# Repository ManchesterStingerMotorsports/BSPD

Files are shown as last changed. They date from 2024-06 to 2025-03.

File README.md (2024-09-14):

# BSPD (Brake System Plausibility Device)

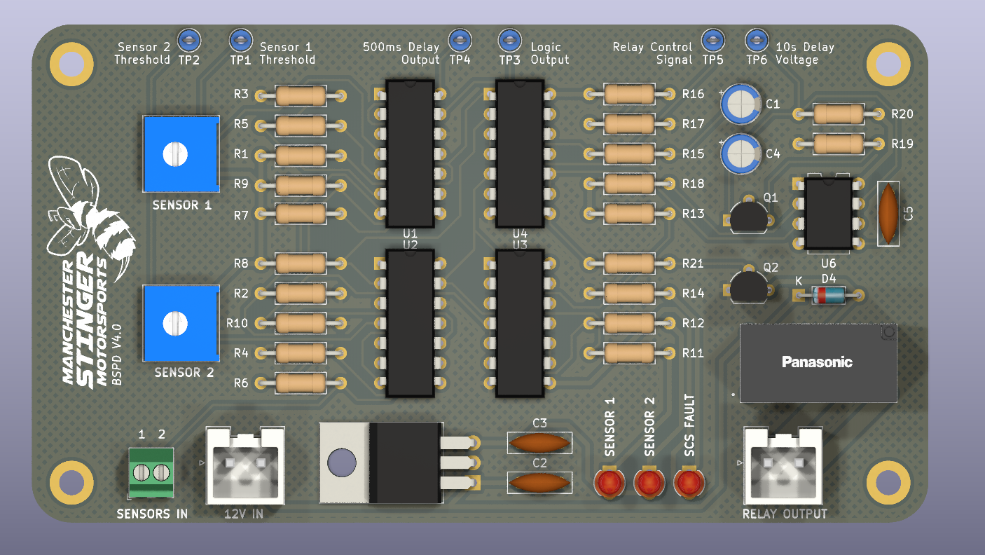
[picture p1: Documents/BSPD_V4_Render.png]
V4.0


[**FULL SCHEMATIC**](Documents/BSPD_V4_Schematic.pdf)

## Working Principle

The diagram below shows how the bspd would work (NOT the actual schematic)

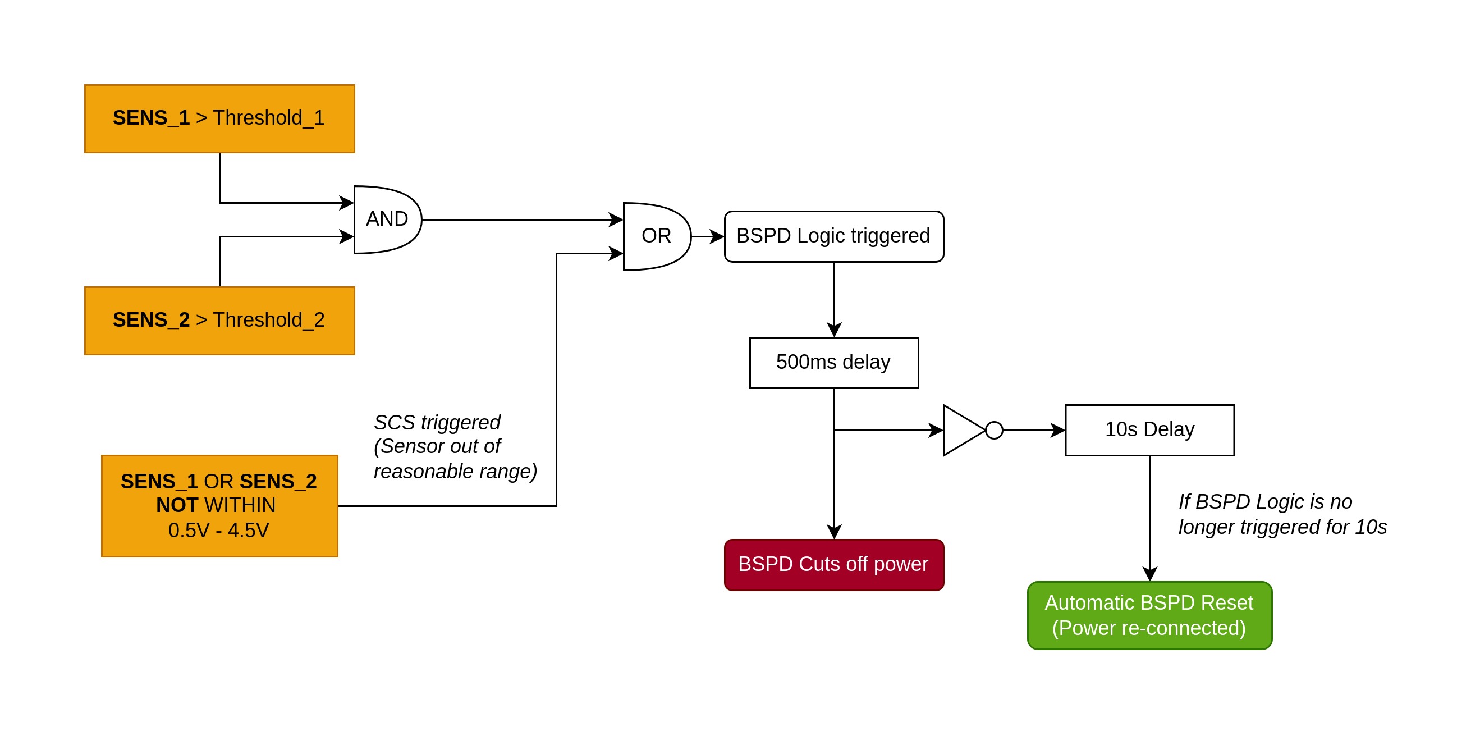
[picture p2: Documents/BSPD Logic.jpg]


- If both sensors' voltage are above the threshold voltage (set using the potentiometer) **or** SCS is triggered -> the bspd will cut off power.
- The delay only triggeres when the input signal is ON for the whole duration (eg, a 200ms signal will be rejected by the 500ms delay)
- The bspd will automatically reset once the triggering signal is no longer present for 10s

## Troubleshooting

There are 3 LEDs and 6 testpoints to be used when troubleshooting

- Sensor 1 or 2 LED turns ON 
  - **CAUSE:** The sensor voltage of 1 or 2 is higher than the threshold
  - Adjust the potentiometer to set the correct voltage threshold while measuring the voltage on TP1 and TP2 (Voltage on the test points should change as the potentiometer is turned).
  - Measure the input sensor voltage (Make sure the sensor is working)

- SCS LED turns ON
  - **CAUSE:** One of the sensors' voltage are outside the range of 0.5V to 4.5V
  - Make sure both sensors are connected (if one of the sensor is disconnected it will trigger the SCS).
  - Measure both sensors voltage to be within the range of 0.5V to 4.5V
  - Try to connect a 2.5V signal to both of the sensor input (The LED should turn off).
  - If all fails, there might be a fault on the scs circuit

- BSPD not resetting after 10s
  - Disconnect anything connected to TP6 (if theres any)
  - Make sure none of the LED is on during the 10s duration
  - Try to test the normal operation of the bspd to ensure that only the 10s delay is not working (chances are there might be other fault that is causing this)

## Important Notes

- For test point 6, TP6 (10s Delay Voltage), probing the point will affect the duration of the 10s delay. This is due to the use of a 1 Mega ohm resistor which is the range of most oscilloscope/multimeter input resistance. Using a 1X probe with an oscilloscope can even prevent the delay from working at all. So, **do not use the TP6 to measure the delay**, instead just use TP5 which is essentially the delay output.
- When manufacturing the board with the uni, have fun finding super small hidden shorted traces (possibly one under silkscreen). For some reason most of the BSPD boards made by the uni always have their own faults so, save yourself from a future headache by testing out the board slowly as you assemble them. **Removing copper pours might help so please remove it for the next revision.**

## Design Choices

Some parts of the schematic might need some extra explanation:

- The comparator LM339 can only reliably compare signals if one signal above 3V (refer the datasheet, look at "common mode range"), so to check for the 4.5V threshold, a voltage divider is used to scale down the input by half.
- The outputs of the comparator is connected together for SCS check since it is an open-drain output which basically OR gate all the outputs together
- The 10s timer uses a 555 monostable retriggerable circuit which we just realised that there is a dedicated IC that does the same thing. Something like SN74LVC1G123, which you might consider for future revision.

## Version Changelog

**V1.0**
- First Routed PCB

**V1.1**
- Changed R26 to 4.7k to limit current to base of the BJT controlling the relay

**V2.0**

- Changes are made after feedback from Dr. Theo
- Changed 500ms timer resistor to 430k with the assumption of 1% tolerence (Expected = 516ms, Min = 511ms, Max = 521ms)
- Changed the current limiting resistors from 470 to 4.7k to limit current to less than 1 mA (NAND gate limit)
- Removed copper pad on the mounting holes and added clearance from other copper pads
- Fixed ground routing loop on the PCB
- Smaller hatched copper pours
- Removed redundant voltage divider for SCS voltage reference

**V3.0**
- Replaced 5V supply input with 12V supply input
- Added 5V Voltage Regulator with capacitors
- Team logo added

**V4.0**
- Changed 5V Reg to a more common LM7805
- Changed transistors footprint to a bigger seperation pads footprint due to uni fabrication limitation
- Changed trimmer to a bigger but more common equivalent alternative
- Added diode for reverse relay coil voltage protection 
- PCB Routing optimised
- Added test points for easier troubleshooting

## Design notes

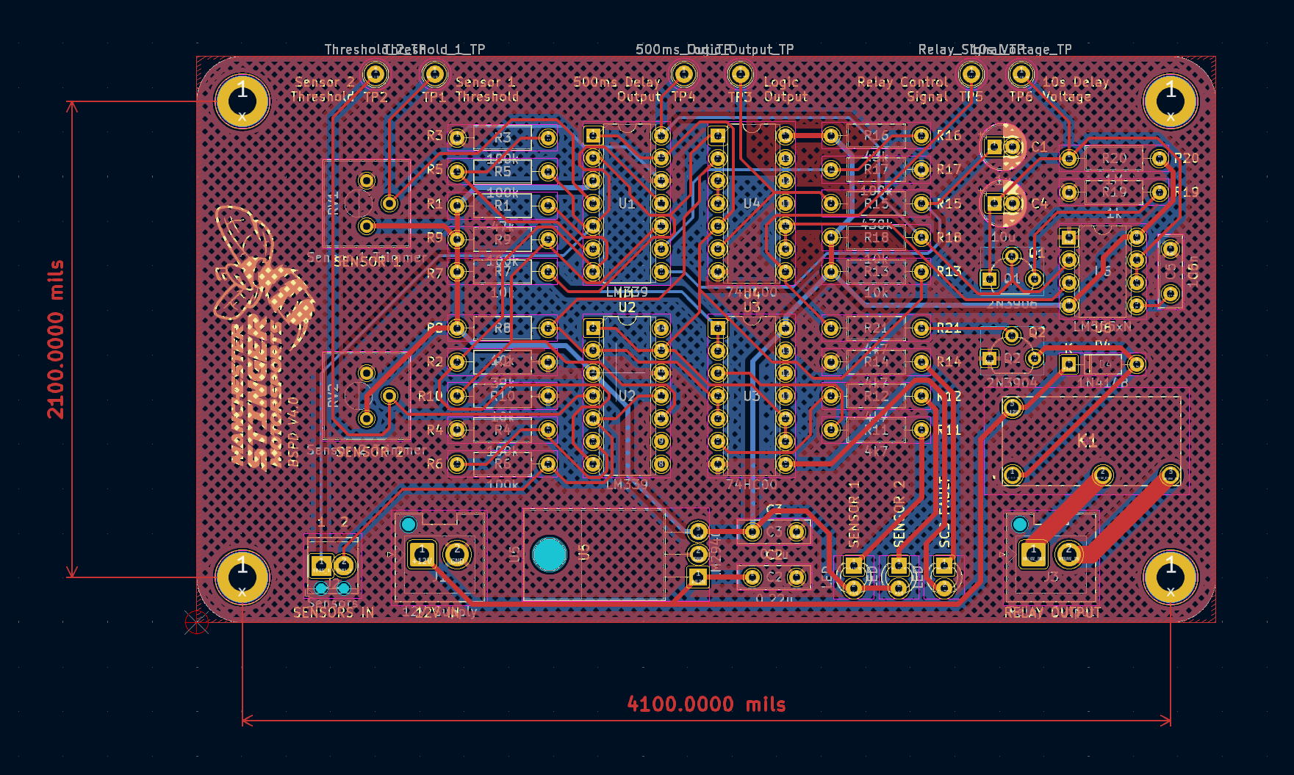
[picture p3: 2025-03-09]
Documents/BSPD Dimensions.png

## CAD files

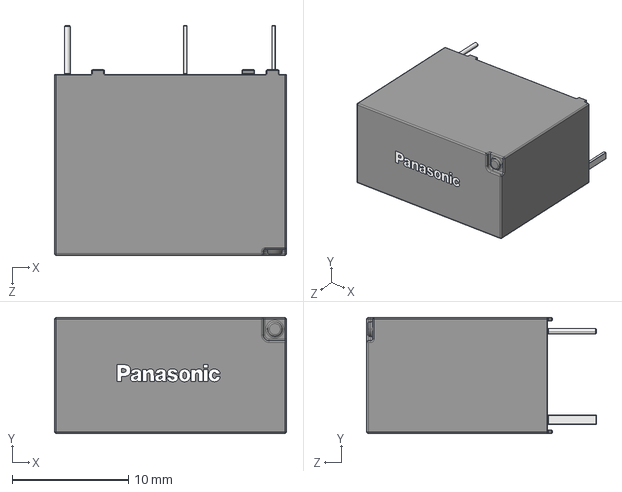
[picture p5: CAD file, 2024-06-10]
BSPD PCB/footprints/3D/ALQ3F12.stp
20.0 x 10.0 x 19.8 mm
ALQ305
Panasonic_Logo_5mm

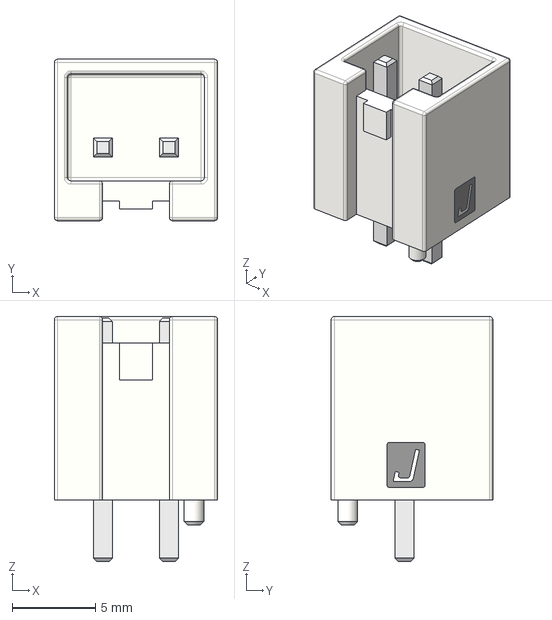
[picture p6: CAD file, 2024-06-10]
BSPD PCB/footprints/3D/B2P-VH-FB-B_LF__SN_.stp
9.80 x 9.70 x 14.7 mm

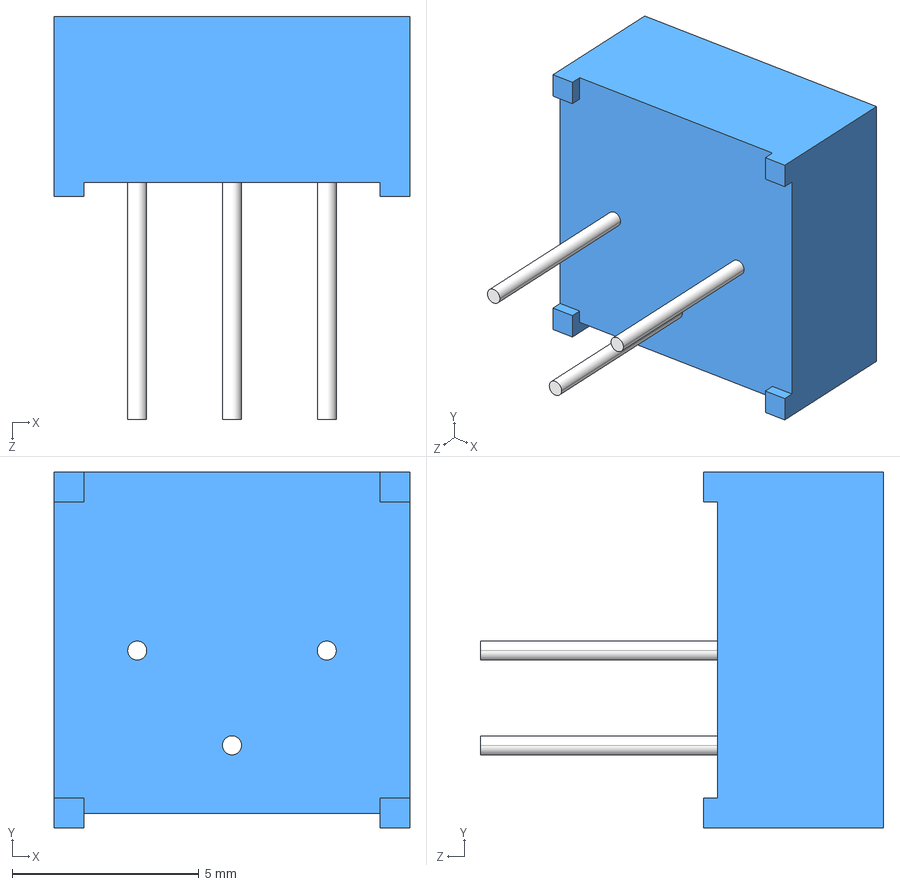
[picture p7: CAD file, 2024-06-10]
BSPD PCB/footprints/3D/3386P-1-500LF.stp
9.53 x 9.53 x 10.8 mm

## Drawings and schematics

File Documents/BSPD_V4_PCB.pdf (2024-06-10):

1 | 2 | 3 | 4 | 5 | 6

A

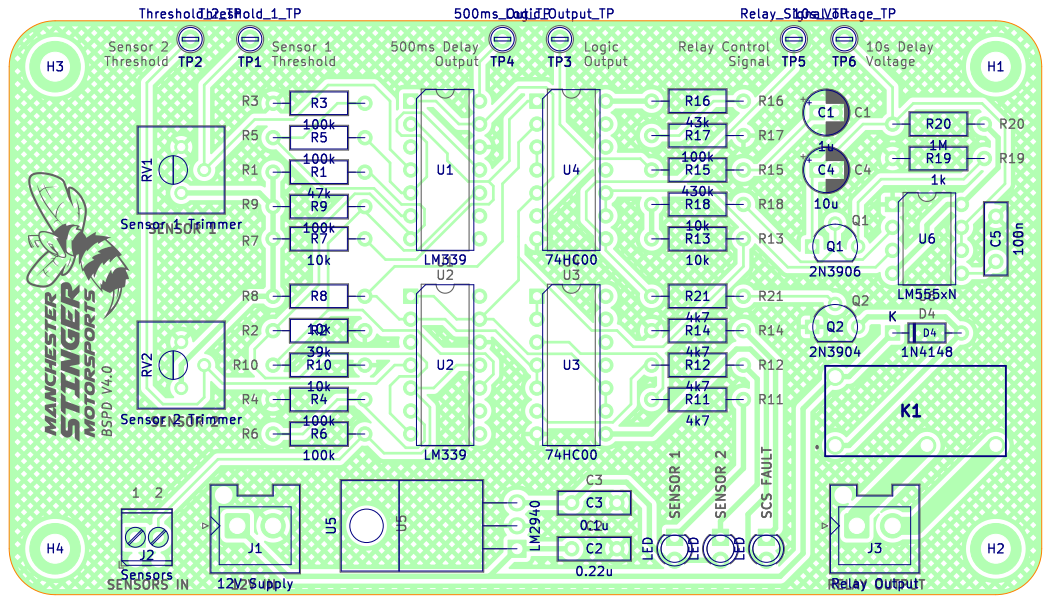
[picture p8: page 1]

Logic Output Sensor 2 Threshold

1 | 2 | 3 | 4 | 5 | 6

A

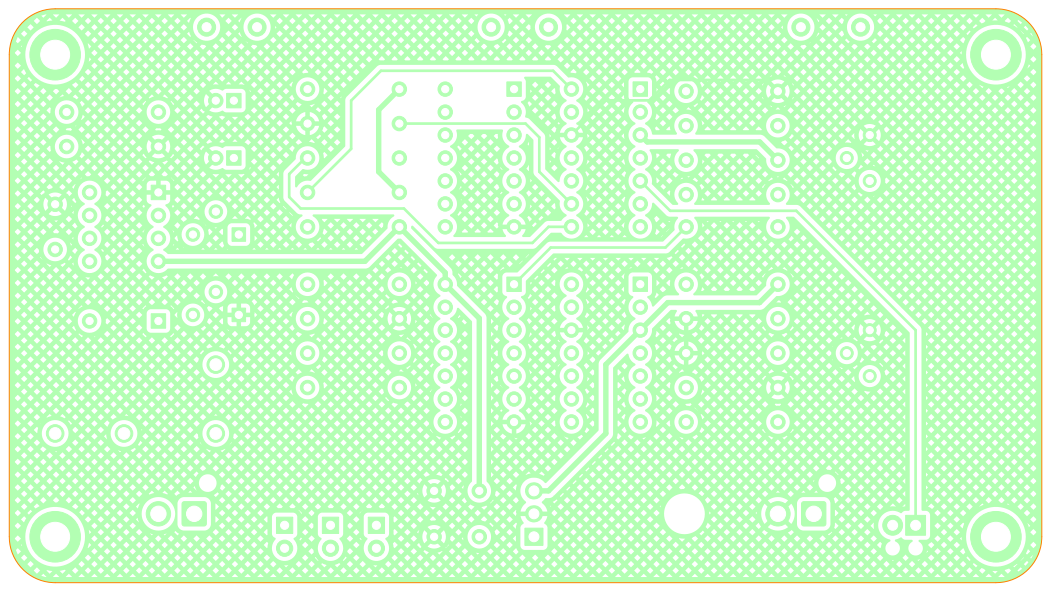
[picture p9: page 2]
D Date: 2024-06-10 KiCad; kicad; 7.0.8 Size: A4; Rev: V4.0; File: BSPD_ManchesterStingerMotorsports.kicad_pcb Sheet: Manchester Stinger; Motorsports

Id: 1/1 Title: BPSD

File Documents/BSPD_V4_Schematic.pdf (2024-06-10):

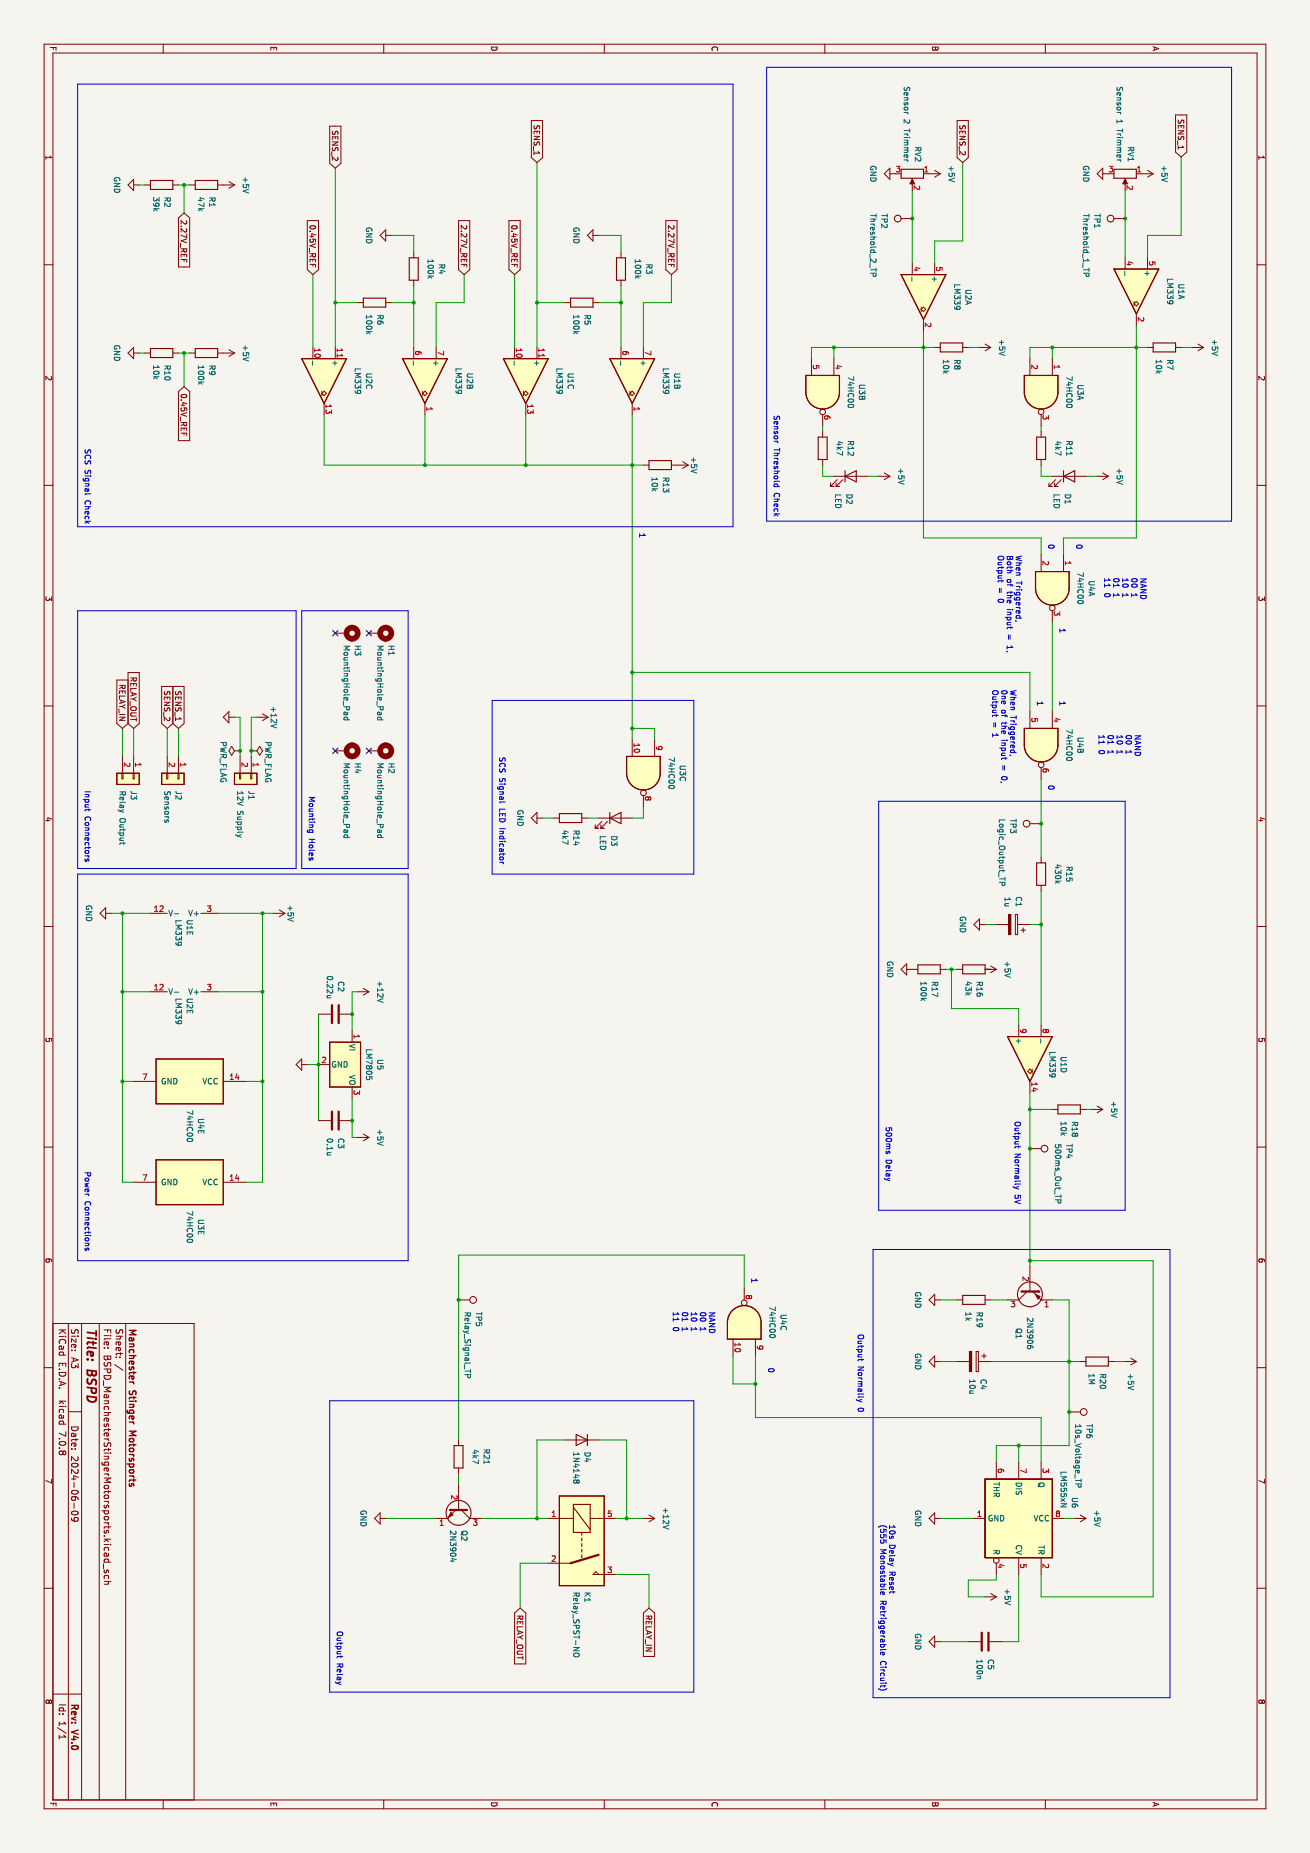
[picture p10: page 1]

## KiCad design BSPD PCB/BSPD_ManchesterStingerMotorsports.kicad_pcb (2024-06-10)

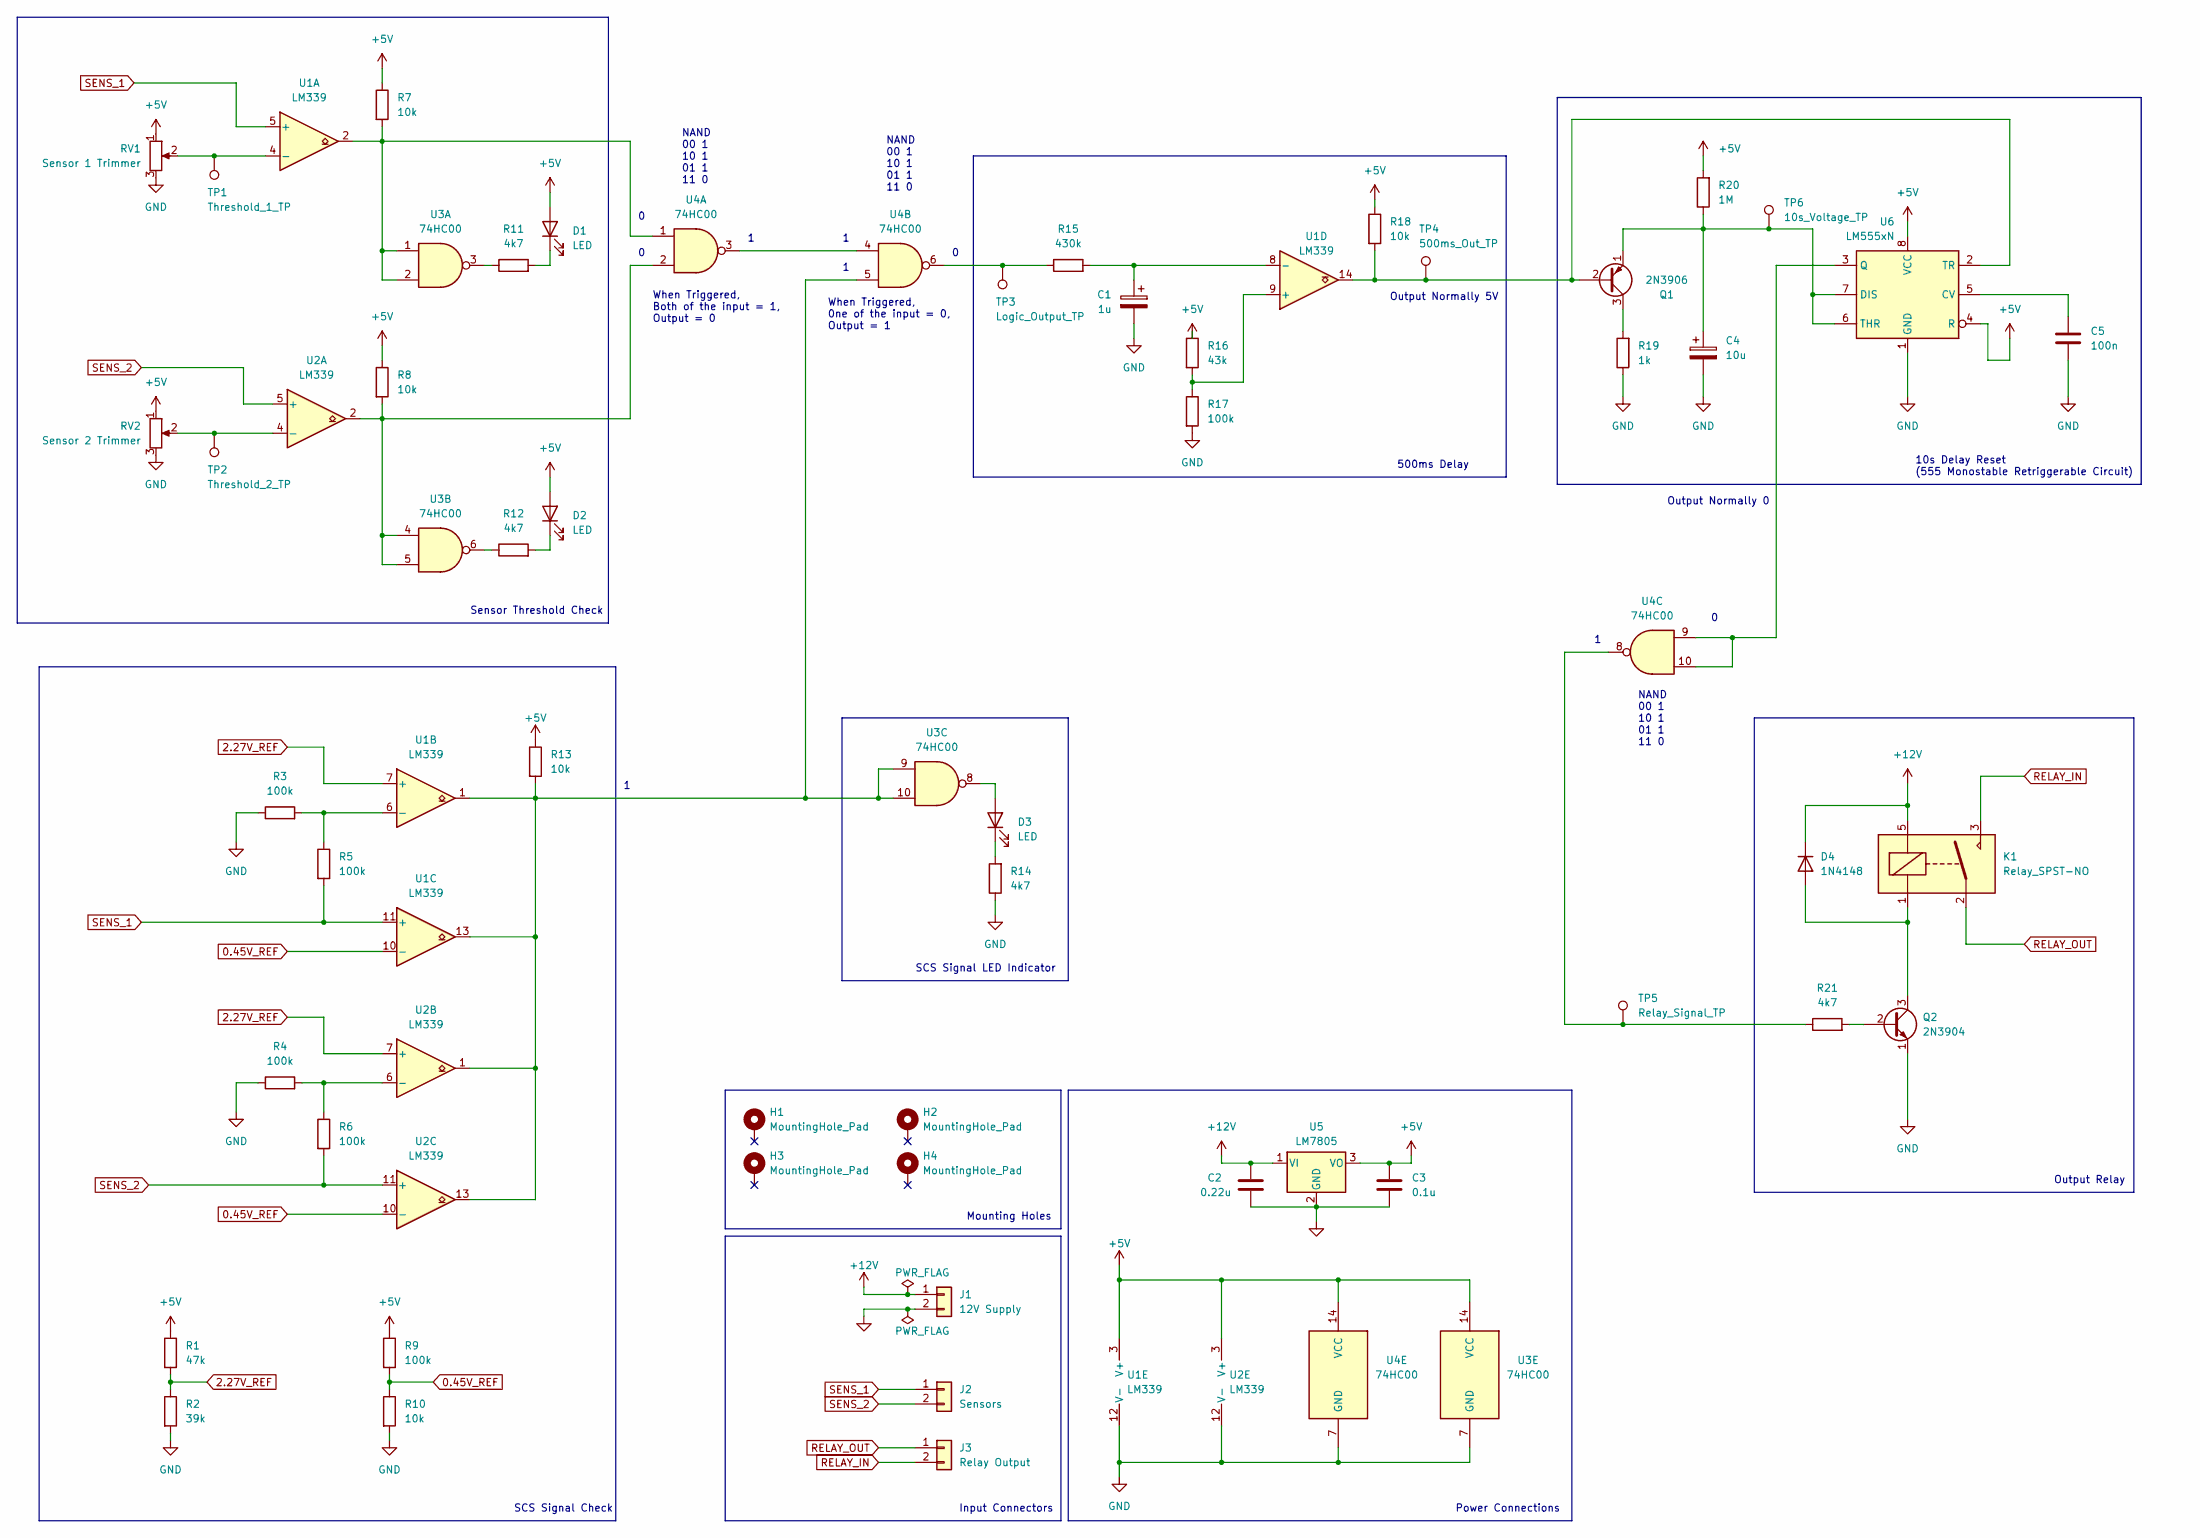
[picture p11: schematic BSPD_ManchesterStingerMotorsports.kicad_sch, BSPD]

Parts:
C1: 1u; CP_Radial_D5.0mm_P2.00mm
C2: 0.22u; C_Disc_D8.0mm_W2.5mm_P5.00mm
C3: 0.1u; C_Disc_D8.0mm_W2.5mm_P5.00mm
C4: 10u; CP_Radial_D5.0mm_P2.00mm
C5: 100n; C_Disc_D8.0mm_W2.5mm_P5.00mm
D1, D2, D3: LED; LED_D3.0mm
D4: 1N4148; D_DO-35_SOD27_P7.62mm_Horizontal
H1, H2, H3, H4: MountingHole_Pad; MountingHole_3.2mm_M3_DIN965_Pad
J1: 12V Supply; JST_VH_B2P-VH-FB-B_1x02_P3.96mm_Vertical
J2: Sensors; TerminalBlock_Phoenix_MPT-0,5-2-2.54_1x02_P2.54mm_Horizontal
J3: Relay Output; JST_VH_B2P-VH-FB-B_1x02_P3.96mm_Vertical
K1: Relay_SPST-NO; ALQ305
Q1: 2N3906; TO-92L_Wide
Q2: 2N3904; TO-92L_Wide
R1: 47k; R_Axial_DIN0207_L6.3mm_D2.5mm_P10.16mm_Horizontal
R2: 39k; R_Axial_DIN0207_L6.3mm_D2.5mm_P10.16mm_Horizontal
R3, R4, R5, R6, R9, R17: 100k; R_Axial_DIN0207_L6.3mm_D2.5mm_P10.16mm_Horizontal
R7, R8, R10, R13, R18: 10k; R_Axial_DIN0207_L6.3mm_D2.5mm_P10.16mm_Horizontal
R11, R12, R14, R21: 4k7; R_Axial_DIN0207_L6.3mm_D2.5mm_P10.16mm_Horizontal
R15: 430k; R_Axial_DIN0207_L6.3mm_D2.5mm_P10.16mm_Horizontal
R16: 43k; R_Axial_DIN0207_L6.3mm_D2.5mm_P10.16mm_Horizontal
R19: 1k; R_Axial_DIN0207_L6.3mm_D2.5mm_P10.16mm_Horizontal
R20: 1M; R_Axial_DIN0207_L6.3mm_D2.5mm_P10.16mm_Horizontal
RV1: Sensor 1 Trimmer; Potentiometer_Bourns_3386P_Vertical
RV2: Sensor 2 Trimmer; Potentiometer_Bourns_3386P_Vertical
TP1: Threshold_1_TP; TestPoint_Loop_D1.80mm_Drill1.0mm_Beaded
TP2: Threshold_2_TP; TestPoint_Loop_D1.80mm_Drill1.0mm_Beaded
TP3: Logic_Output_TP; TestPoint_Loop_D1.80mm_Drill1.0mm_Beaded
TP4: 500ms_Out_TP; TestPoint_Loop_D1.80mm_Drill1.0mm_Beaded
TP5: Relay_Signal_TP; TestPoint_Loop_D1.80mm_Drill1.0mm_Beaded
TP6: 10s_Voltage_TP; TestPoint_Loop_D1.80mm_Drill1.0mm_Beaded
U1, U2: LM339; DIP-14_W7.62mm
U3, U4: 74HC00; DIP-14_W7.62mm
U5: LM7805; TO-220-3_Horizontal_TabDown
U6: LM555xN; DIP-8_W7.62mm

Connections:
0.45V_REF: R9.2, R10.1, U1.10 (-), U2.10 (-)
2.27V_REF: R1.2, R2.1, U1.7 (+), U2.7 (+)
+5V: C3.1, D1.2 (A), D2.2 (A), R1.1, R7.1, R8.1, R9.1, R13.1, R16.1, R18.1, R20.2, RV1.1, RV2.1, U1.3 (V+), U2.3 (V+), U3.14 (VCC), U4.14 (VCC), U5.3 (VO), U6.4 (R), U6.8 (VCC)
+12V: C2.1, D4.1 (K), J1.1, K1.5, U5.1 (VI)
GND: C1.2, C2.2, C3.2, C4.2, C5.2, J1.2, Q2.1 (E), R2.2, R3.1, R4.1, R10.2, R14.1, R17.2, R19.1, RV1.3, RV2.3, U1.12 (V-), U2.12 (V-), U3.7 (GND), U4.7 (GND), U5.2 (GND), U6.1 (GND)
unnamed: D1.1 (K), R11.2
unnamed: D2.1 (K), R12.2
unnamed: D3.2 (A), U3.8
unnamed: D3.1 (K), R14.2
unnamed: D4.2 (A), K1.1, Q2.3 (C)
unnamed: Q1.2 (B), R18.2, TP4.1, U1.14, U6.2 (TR)
unnamed: Q1.3 (C), R19.2
unnamed: C4.1, Q1.1 (E), R20.1, TP6.1, U6.6 (THR), U6.7 (DIS)
unnamed: Q2.2 (B), R21.2
unnamed: R7.2, U1.2, U3.1, U3.2, U4.1
unnamed: R8.2, U2.2, U3.4, U3.5, U4.2
unnamed: R11.1, U3.3
unnamed: R12.1, U3.6
unnamed: R13.2, U1.1, U1.13, U2.1, U2.13, U3.9, U3.10, U4.5
unnamed: R15.1, TP3.1, U4.6
unnamed: R21.1, TP5.1, U4.8
unnamed: RV1.2, TP1.1, U1.4 (-)
unnamed: R3.2, R5.1, U1.6 (-)
unnamed: R16.2, R17.1, U1.9 (+)
unnamed: C1.1, R15.2, U1.8 (-)
unnamed: RV2.2, TP2.1, U2.4 (-)
unnamed: R4.2, R6.1, U2.6 (-)
unnamed: U4.3, U4.4
unnamed: C5.1, U6.5 (CV)
unnamed: U4.9, U4.10, U6.3 (Q)
RELAY_IN: J3.2, K1.3
RELAY_OUT: J3.1, K1.2
SENS_1: J2.1, R5.2, U1.5 (+), U1.11 (+)
SENS_2: J2.2, R6.2, U2.5 (+), U2.11 (+)

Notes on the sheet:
SCS Signal Check
When Triggered, Both of the input = 1, Output = 0
500ms Delay
Mounting Holes
Output Relay
SCS Signal LED Indicator
Power Connections
NAND 00 1 10 1 01 1 11 0
Sensor Threshold Check
Output Normally 5V
Input Connectors
When Triggered, 0ne of the input = 0, Output = 1
10s Delay Reset (555 Monostable Retriggerable Circuit)
Output Normally 0

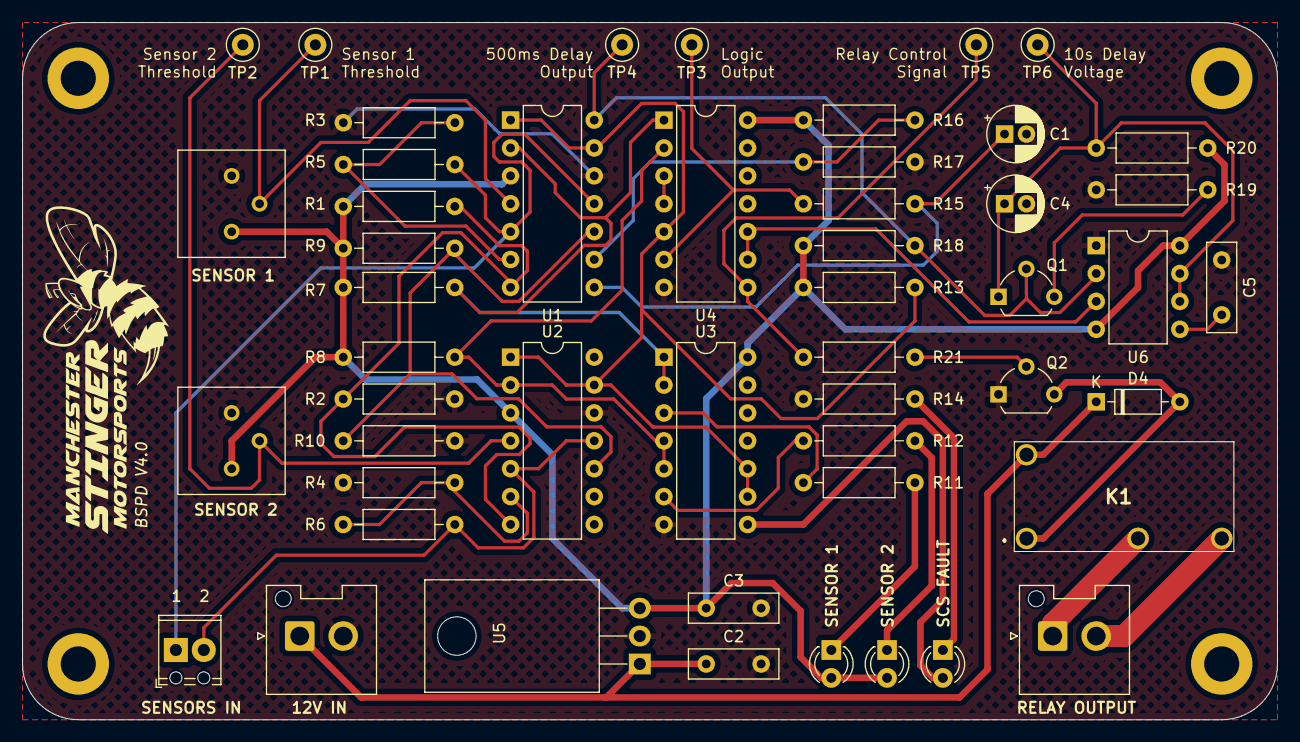
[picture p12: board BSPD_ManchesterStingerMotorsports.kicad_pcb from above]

Board: 2 copper layers, 114.3 x 63.5 mm, 54 parts (0 on the bottom side), 34 nets.

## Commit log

2024-06-10 first commit V4.0
    [3386P-1-500LF.stp, ALQ3F12.stp, B2P-VH-FB-B_LF__SN_.stp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]
2025-03-09 added bspd mounting hole dimensions
